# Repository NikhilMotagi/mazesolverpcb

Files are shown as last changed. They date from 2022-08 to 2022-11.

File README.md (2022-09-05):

#                                                                     MILLI MOUSE

This repo is for pcbs that were designed for mazesolver MILLIMOUSE (RIP)

The project went through many changes, some were minor some were major. Following are short discriptions about each design.

## MAZESOLVERWITHIR

u(mew)controller of choice was STM32F103C8T6 , because why not, it is faster than Arduino and has a bigger storage.

Here IR sensors acted as proximity sensors. They woud send signals when walls are in a given range.

RGB led was used to give indications and also to flash like police strobe light becuase why not *FLEXXXXXX*(later it was understood "why not").

MPU6050 was used to get orientations of the bot, so that perfect 90 degree turns could be performed.

Battery - 7.4V 2S lipo orange battery, a buck converter was used to step it down to 5V. 

Points to be noted--> 

1)IR won't always work as intended and calibaration is a nightmare as the readings change with ambient light.
2) Do not flip the PCB print while exporting PDF for both back copper. Only valid for text 

## MAZESOLVERSTM32_ULTRASONIC

KNOCK KNOCK 

Who's there ?

Ambient light 

IR's were not the greatest choice for checking distance, also there was concern about centering the bot.

SO here comes the new component HC-SR04!



The pcb had to be redesigned for ultrasonic and this time for good, the placement were done using dxf files from cad so everything was perfect.

WhatsApp Image 2022-09-05 at 15 48 17

Other unsophisticated yet time saving efforts were also explored(We all agreed pcb is the way to go).

WhatsApp Image 2022-08-08 at 16 50 47

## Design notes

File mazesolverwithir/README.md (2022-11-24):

The design inculdes stm32 microcontroller aka sasta controller, IR sensors, L9110s Motor driver, N20 encoder motors, MPU6050.

Working -
IR sensors are set to give signal for a certain distance. MPU is used to get angle of rotation for precise 90 degree turns. Encoder motors help in counting how far the 
bot has travelled 

STM32 is prefered because of it's high operation speed and comparatively good storage.

maz1

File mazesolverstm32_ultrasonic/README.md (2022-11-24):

The bot had a major component change in this version. Instead of IR sensors Ultrasonic sensors were used. With this change a next layout had to be created. 
While making this new desing a new practice was implemented - using dxf files for edgecut and silkscreen. This helped a lot Kicad as of now is not that comfortable for precise placement and also why not use CAD softwares.

maze

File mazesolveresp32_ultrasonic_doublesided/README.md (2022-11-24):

This version of pcb has no component changes. A new thing that we tried was to design and fabricate a double sided pcb .
Points to be remebered are 
1) Keep the track width more than 1mm because these are not easy to DIY.
2) Remember to provide appropriate diameter vias when needed, professionally manufactured pcbs have revets that join both bottom and top layers.  

MilliMousePCB3d

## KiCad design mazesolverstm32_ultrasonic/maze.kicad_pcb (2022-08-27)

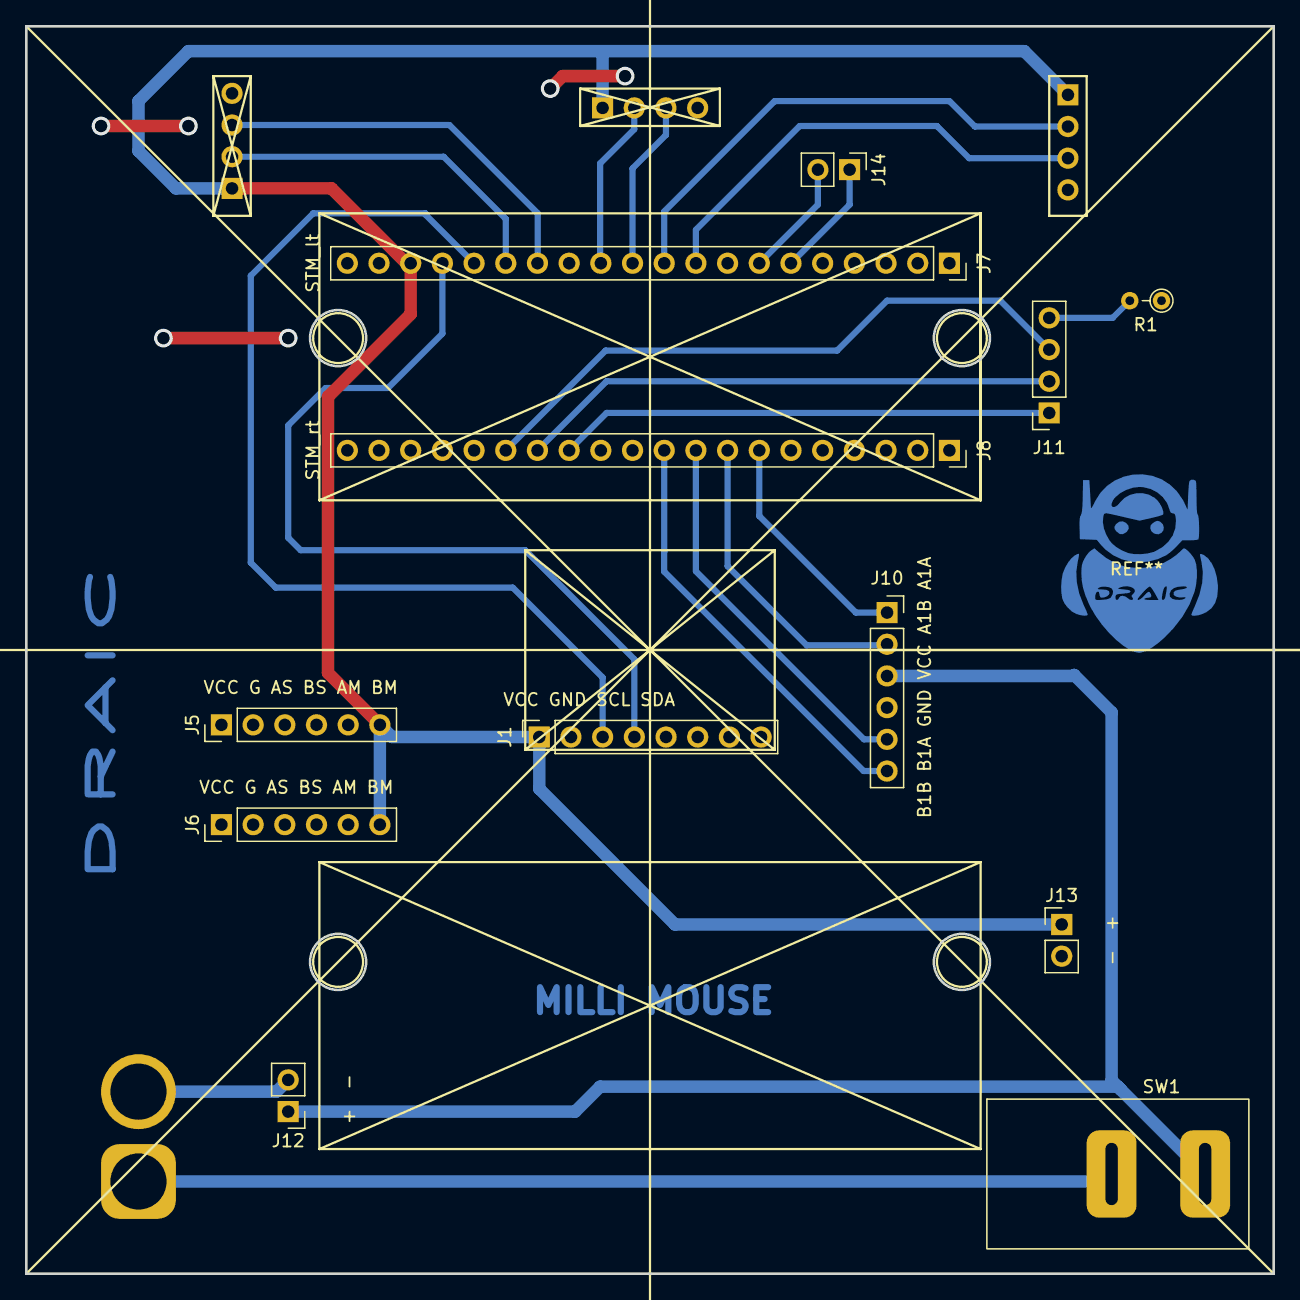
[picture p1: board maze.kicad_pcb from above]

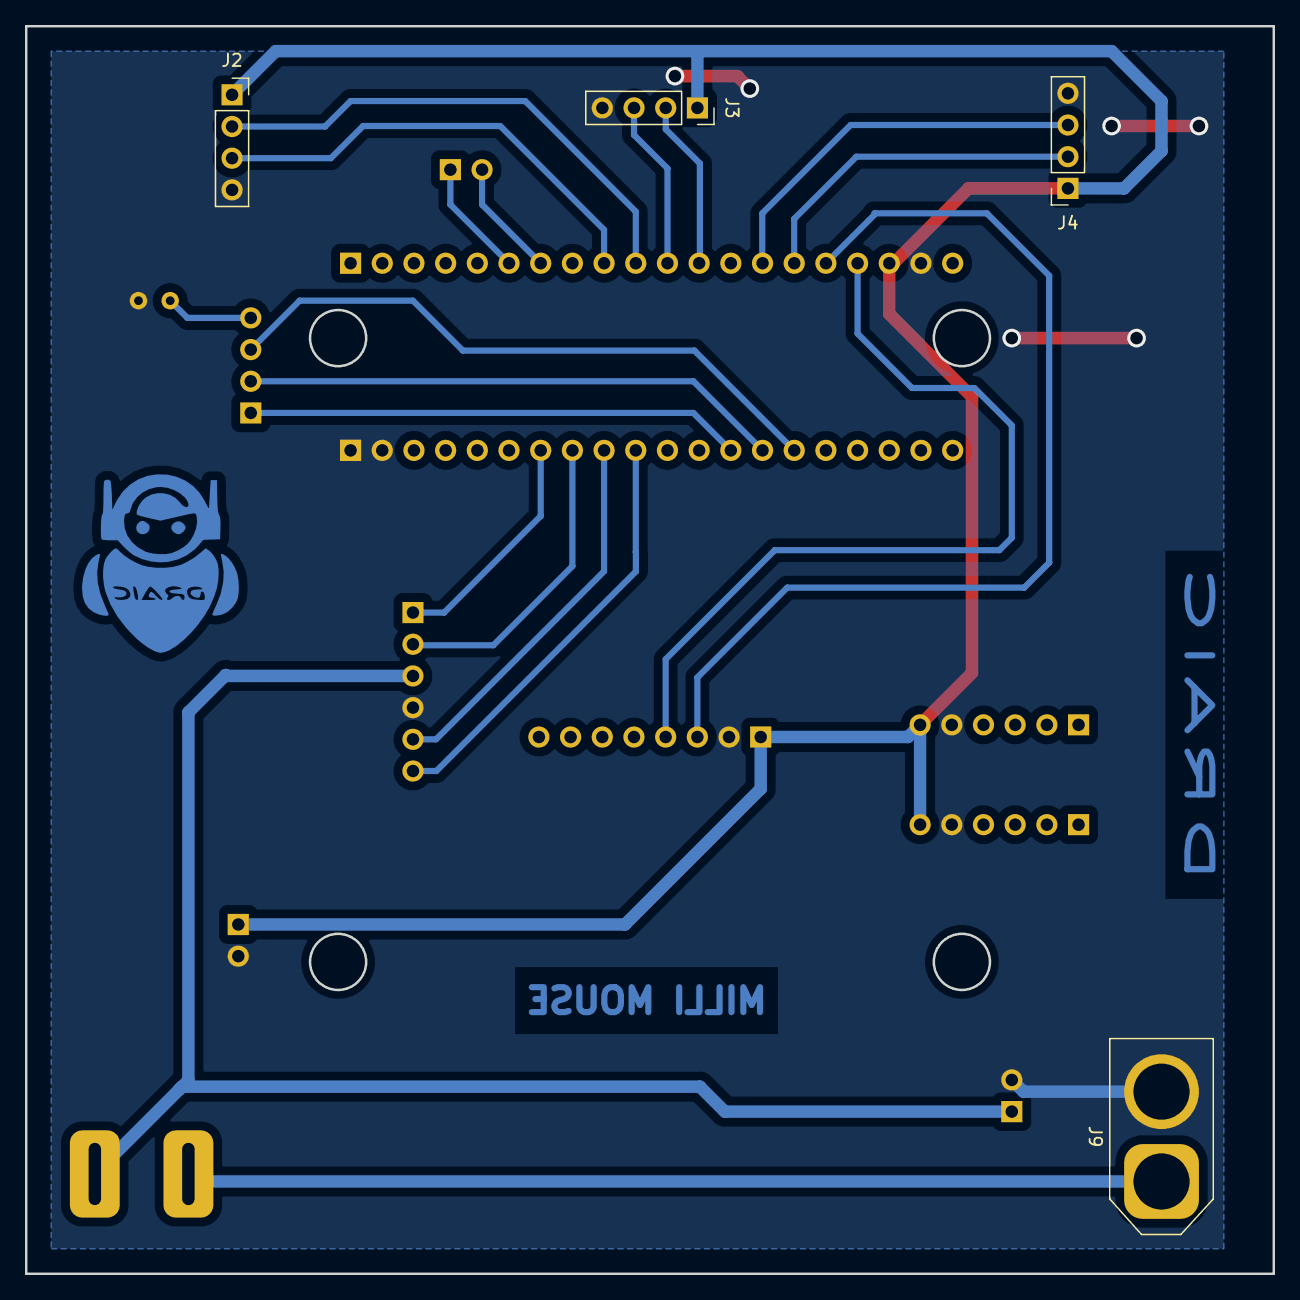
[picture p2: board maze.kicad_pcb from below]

Board: 2 copper layers, 100.0 x 100.0 mm, 16 parts (4 on the bottom side), 22 nets.

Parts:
J1: VCC GND SCL SDA; PinSocket_1x08_P2.54mm_Vertical
J2: US_1; PinSocket_1x04_P2.54mm_Vertical
J3: US_2; PinSocket_1x04_P2.54mm_Vertical
J4: US_3; PinSocket_1x04_P2.54mm_Vertical
J5, J6: VCC G AS BS AM BM; PinHeader_1x06_P2.54mm_Vertical
J7: STM_lt; PinSocket_1x20_P2.54mm_Vertical
J8: STM_rt; PinSocket_1x20_P2.54mm_Vertical
J9: XT60; AMASS_XT60-M_1x02_P7.20mm_Vertical
J10: B1B B1A GND VCC A1B A1A; PinSocket_1x06_P2.54mm_Vertical
J11: RGB; PinSocket_1x04_P2.54mm_Vertical
J12, J13: - +; PinHeader_1x02_P2.54mm_Vertical
J14: RX TX; PinHeader_1x02_P2.54mm_Vertical
R1: 220; R_Axial_DIN0204_L3.6mm_D1.6mm_P2.54mm_Vertical
SW1: SW_DIP_x01; DPDT_SW

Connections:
A1A: J8.9, J10.5
A1B: J8.10, J10.6
B: J8.15, J11.3
B1A: J8.7, J10.1
B1B: J8.8, J10.2
ECHO_1: J2.3, J7.9
ECHO_2: J3.3, J7.11
ECHO_3: J4.3, J7.14
G: J8.14, J11.2
GND: J1.2, J2.4, J3.4, J4.4, J5.5, J6.5, J7.19, J8.1, J8.2, J9.2, J10.4, J12.2, J13.2, R1.1
unnamed: J9.1, SW1.1
unnamed: J11.4, R1.2
unnamed: J7.6, J14.1
unnamed: J7.7, J14.2
R: J8.13, J11.1
SCL: J1.3, J7.16
SDA: J1.4, J7.17
TRIG_1: J2.2, J7.10
TRIG_2: J3.2, J7.12
TRIG_3: J4.2, J7.15
VCC_5: J1.1, J2.1, J3.1, J4.1, J5.6, J6.6, J7.18, J13.1
VCC_12: J10.3, J12.1, SW1.2

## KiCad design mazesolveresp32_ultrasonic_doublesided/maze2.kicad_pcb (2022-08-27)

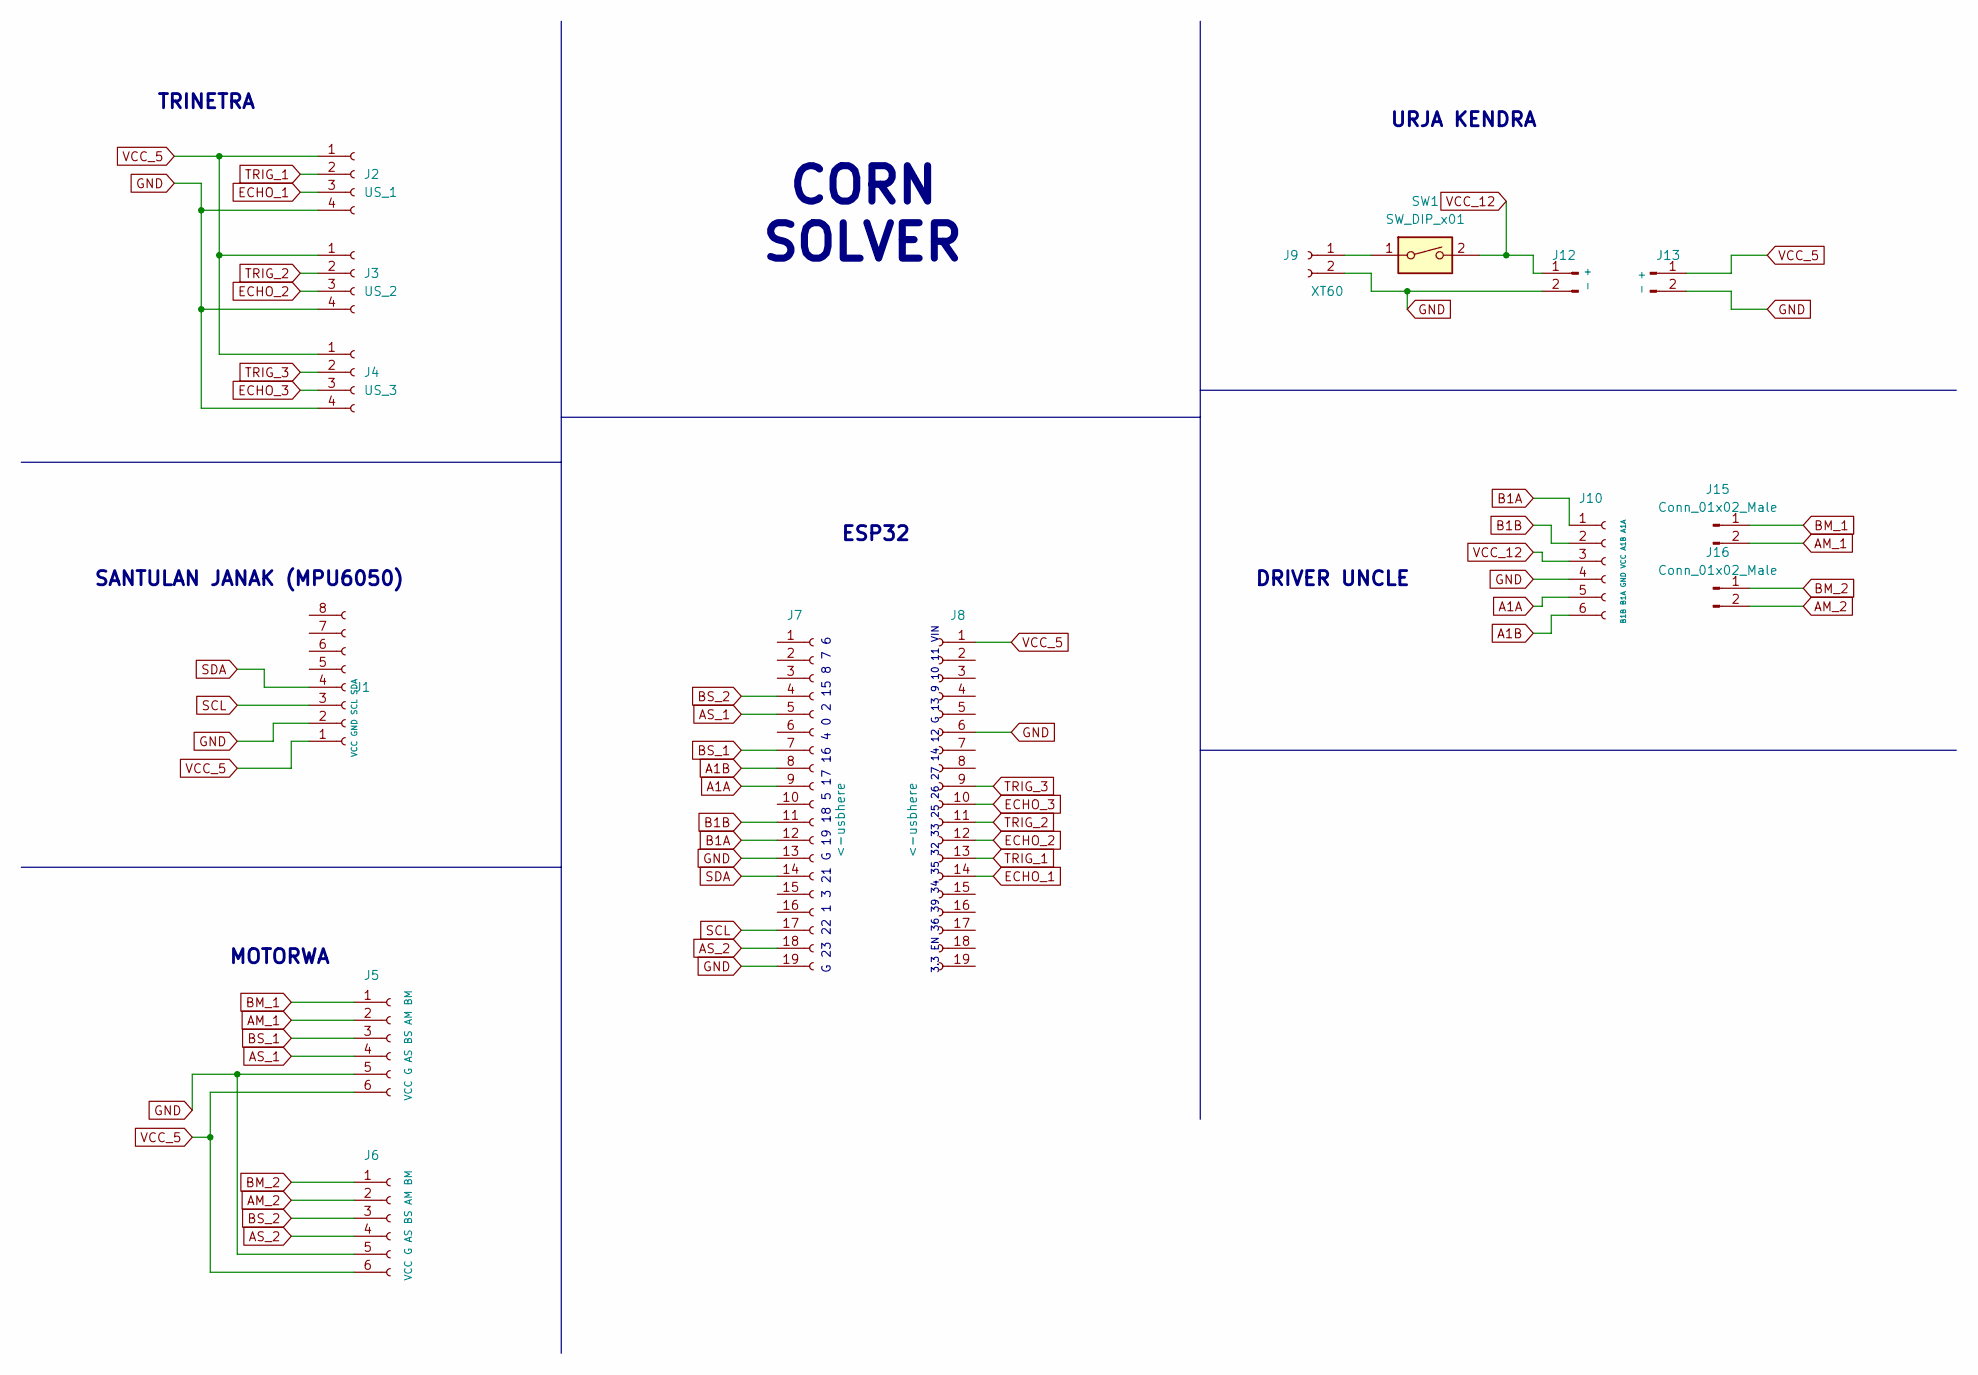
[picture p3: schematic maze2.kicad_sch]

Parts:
J1: VCC GND SCL SDA; PinSocket_1x08_P2.54mm_Vertical
J2: US_1; PinSocket_1x04_P2.54mm_Vertical
J3: US_2; PinSocket_1x04_P2.54mm_Vertical
J4: US_3; PinSocket_1x04_P2.54mm_Vertical
J5, J6: VCC G AS BS AM BM; PinHeader_1x06_P2.54mm_Vertical
J7, J8: <-usbhere; PinSocket_1x19_P2.54mm_Vertical
J9: XT60; AMASS_XT60-M_1x02_P7.20mm_Vertical
J10: B1B B1A GND VCC A1B A1A; PinSocket_1x06_P2.54mm_Vertical
J12, J13: - +; PinHeader_1x02_P2.54mm_Vertical
J15, J16: Conn_01x02_Male; PinSocket_1x02_P2.54mm_Vertical
SW1: SW_DIP_x01; DPDT_SW

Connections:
A1A: J7.9, J10.5
A1B: J7.8, J10.6
AM_1: J5.2, J15.2
AM_2: J6.2, J16.2
AS_1: J5.4, J7.5
AS_2: J6.4, J7.18
B1A: J7.12, J10.1
B1B: J7.11, J10.2
BM_1: J5.1, J15.1
BM_2: J6.1, J16.1
BS_1: J5.3, J7.7
BS_2: J6.3, J7.4
ECHO_1: J2.3, J8.14
ECHO_2: J3.3, J8.12
ECHO_3: J4.3, J8.10
GND: J1.2, J2.4, J3.4, J4.4, J5.5, J6.5, J7.13, J7.19, J8.6, J9.2, J10.4, J12.2, J13.2
unnamed: J9.1, SW1.1
SCL: J1.3, J7.17
SDA: J1.4, J7.14
TRIG_1: J2.2, J8.13
TRIG_2: J3.2, J8.11
TRIG_3: J4.2, J8.9
VCC_5: J1.1, J2.1, J3.1, J4.1, J5.6, J6.6, J8.1, J13.1
VCC_12: J10.3, J12.1, SW1.2

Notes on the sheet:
DRIVER UNCLE
3.3 EN 36 39 34 35 32 33 25 26 27 14 12 G 13 9 10 11 VIN
URJA KENDRA
CORN SOLVER
ESP32
G 23 22 1 3 21 G 19 18 5 17 16 4 0 2 15 8 7 6
SANTULAN JANAK (MPU6050)
MOTORWA
TRINETRA

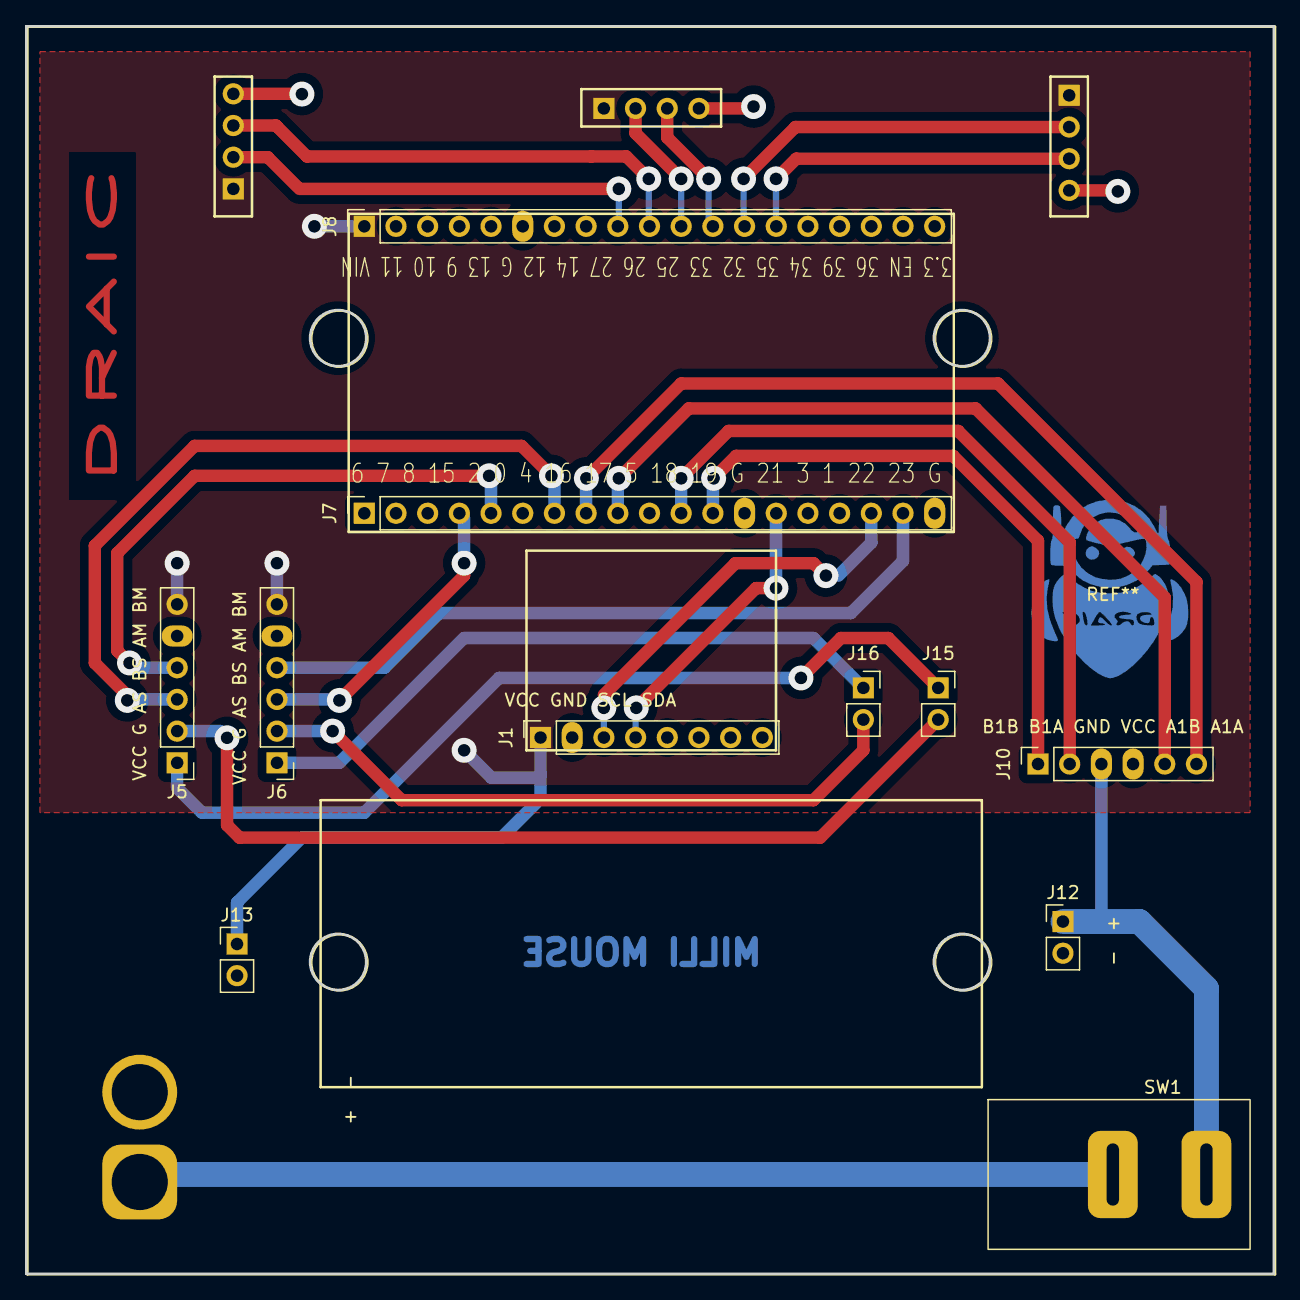
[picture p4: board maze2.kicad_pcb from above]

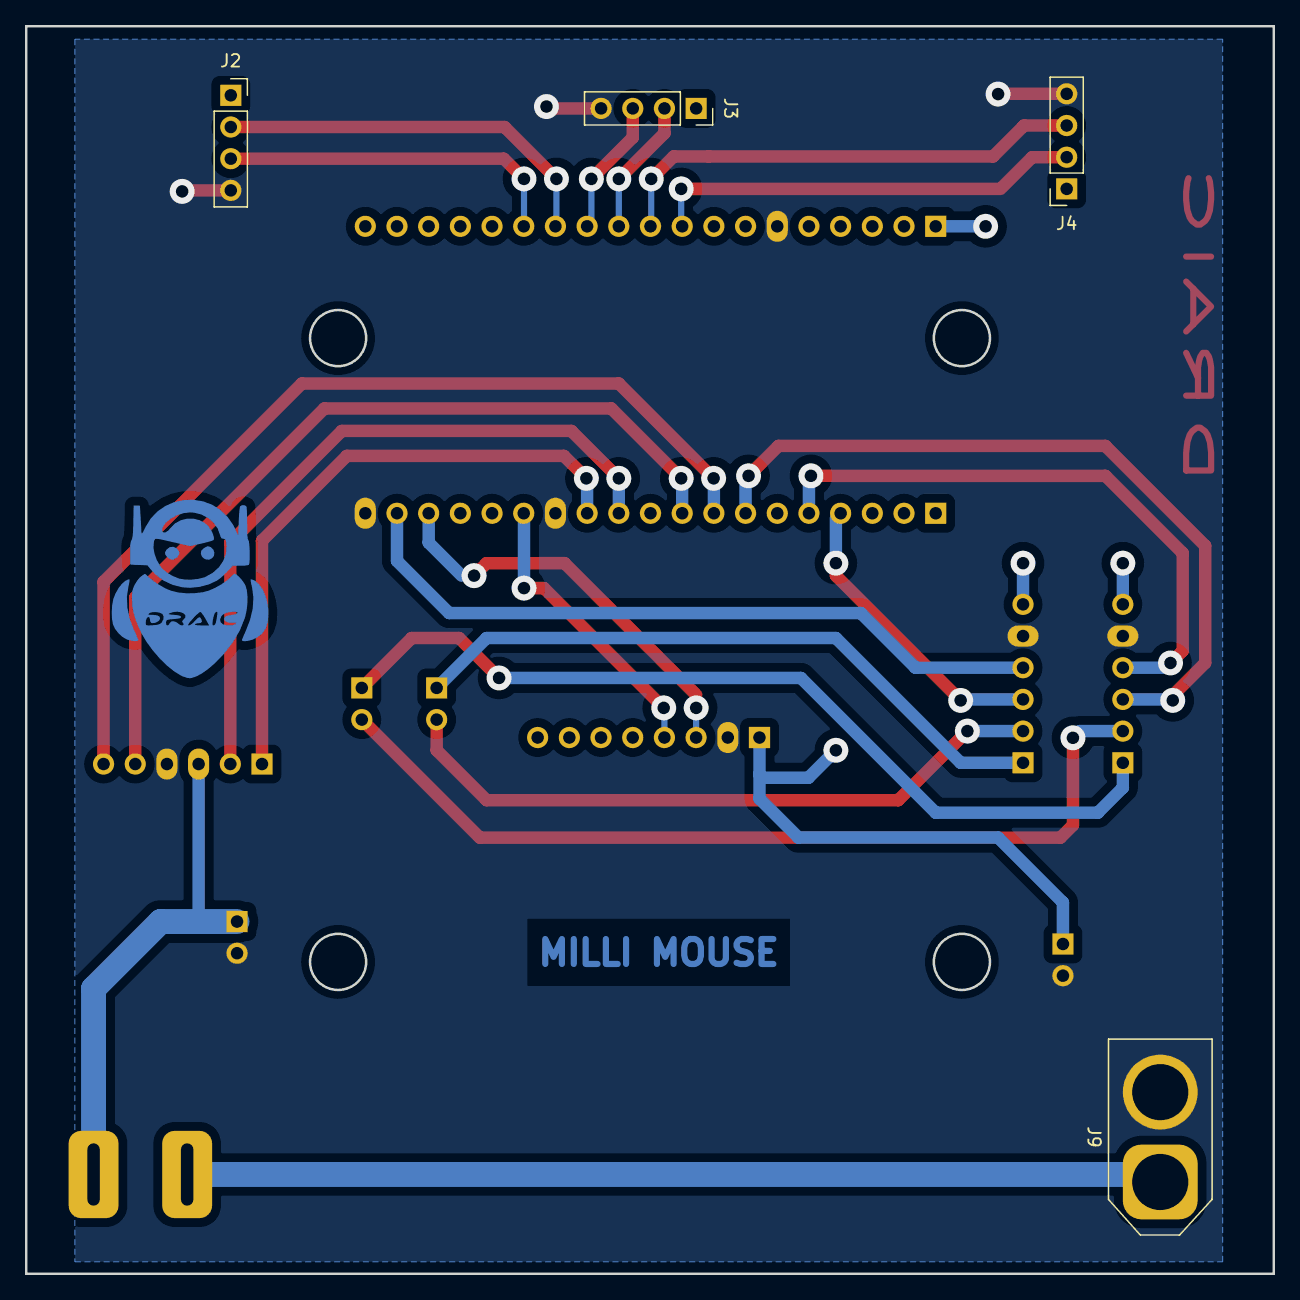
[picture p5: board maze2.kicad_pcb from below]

Board: 2 copper layers, 100.0 x 100.0 mm, 15 parts (4 on the bottom side), 24 nets.

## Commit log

2022-08-27 this is the first design
    [maz1.kicad_pcb, maz1.kicad_sch]
2022-08-27 next versions
    [maze.kicad_pcb, maze.kicad_sch, maze2.kicad_pcb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]
